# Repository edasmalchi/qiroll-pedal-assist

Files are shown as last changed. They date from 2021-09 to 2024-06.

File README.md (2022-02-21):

# qiroll-pedal-assist
#### External pedal-assist system for Qiroll ebike kit, implemented with CMOS digital logic

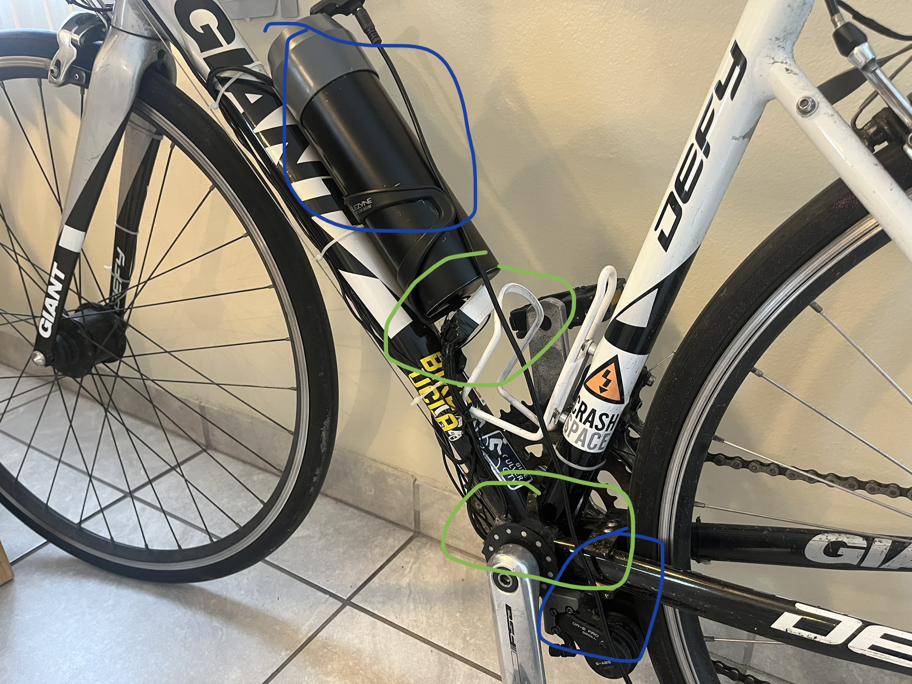
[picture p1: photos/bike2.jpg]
bike


So I got this Qiroll friction-drive ebike kit  to put on my commuter bike. I'd reccomend the [pro](https://www.aliexpress.com/item/1005002975061464.html) [version](https://www.ebay.com/itm/Electric-Bicycle-E-BIKE-Conversion-Kit-QiROLL-Friction-Drive-QR-E-PRO-H70/402658347675) (about $600 shipped), but the standard [kit](https://www.aliexpress.com/item/4000366510773.html) (about $450 shipped) is still around. With light pedaling, the pro version on my bike cruises at about 23mph with about 20 miles of range, while the standard kit delivers about 19mph and about 20 miles (with the larger B70 battery).

The lack of any sort of pedal assist bothered me, with the original design you have to hold down a switch to keep the motor on. (It's a simple switch, not a real throttle so the motor is either on or off. There is a way to select between a lower power mode and a higher power mode.)

This project aims to add pedal assist functionality to the Qiroll kit. I'm using this 12-magnet pedal assist [sensor](https://smile.amazon.com/gp/product/B08GY819YF/), although similar products could work too. The project also supports an optional brake sensor, I'm using [this one](https://www.aliexpress.com/item/4000445394702.html) but others likely work as well. Be sure to verify proper operation in case yours works differently.

#### Hardware Mods
* Since my design needs only one button, with single-clicks turning pedal assist on/off and double-clicks switching controller modes (and/or enabling regen), I didn't need the second button in the original Qiroll switch. So I desoldered it, and used the space/wiring for a resistor and an led that lines up nicely with the hole left by taking the button out, letting me see if pedal assist is currently on or off!

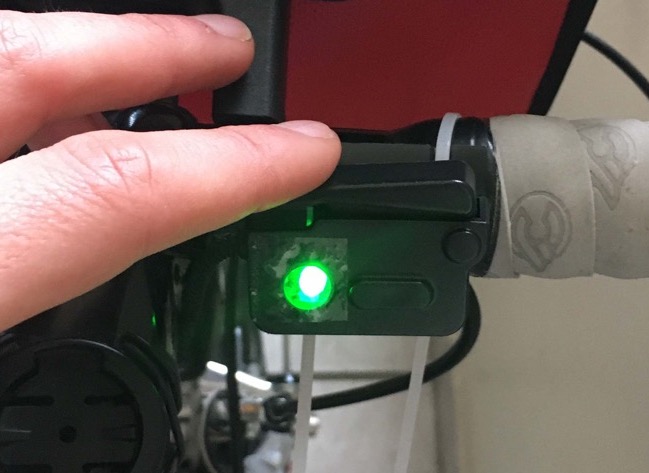
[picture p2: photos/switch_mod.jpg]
switch with LED added


* Stripped the insulation and soldered into one of the battery wires to tap power-- should be fine since the pedal assist system uses very little current but be careful not to damage the battery wire itself. Alternatively you could get some of those Amass connectors it uses and make an adaptor.
* Depending on your setup, cable strain at the battery connector seems to be an issue. Reccomend adding extra strain relief here, and consider tapping at the motor connection instead since splicing in another wire with solder does weaken things.

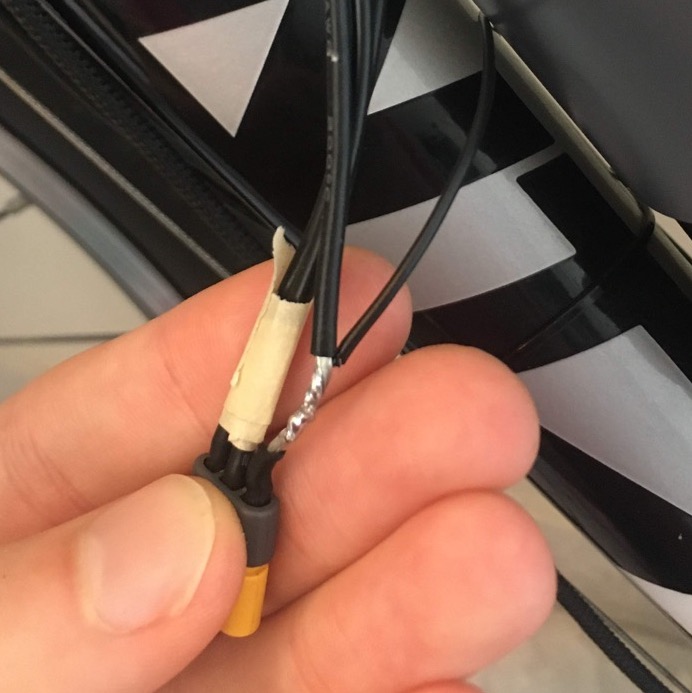
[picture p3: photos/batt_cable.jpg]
battery cable showing small wire soldered to + wire


#### Notes
* The sensor I got reads in both directions, so it will trigger on backwards pedaling as well. I don't think this is a big deal, but there may be sensors out there that only read in one direction.
* After much investigation, the power from the Qiroll micro-usb switch port seems to fluctuate quite a bit. So the reliable thing to do is tap into the + side of the battery, using a linear voltage regulator (or buck converter) to drop down the battery voltage.
* ___Use at your own risk! I reccomend extensive testing of whatever implementation you come up with, ensuring your brakes can stop the bike even if the motor sticks on, and having the battery cable within reach to disconnect if necessary!___

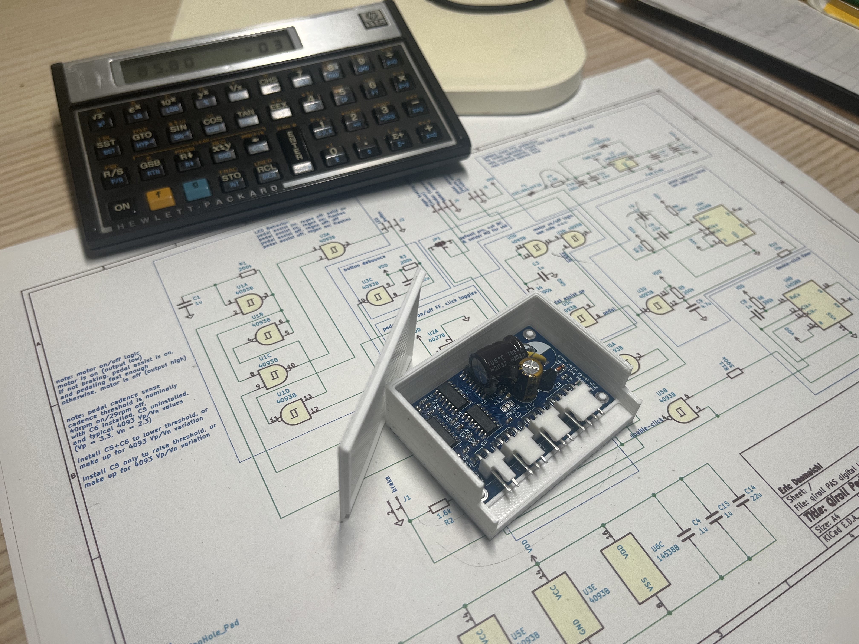
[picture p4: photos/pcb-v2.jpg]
pcb


#### Progress
* Digital logic version 2.5 builds on 2.2 with usability improvements and taillight connector option
* A simple case for 3d printing
* Stripped-down "simple" digital logic version with through-hole components in case that better meets your needs

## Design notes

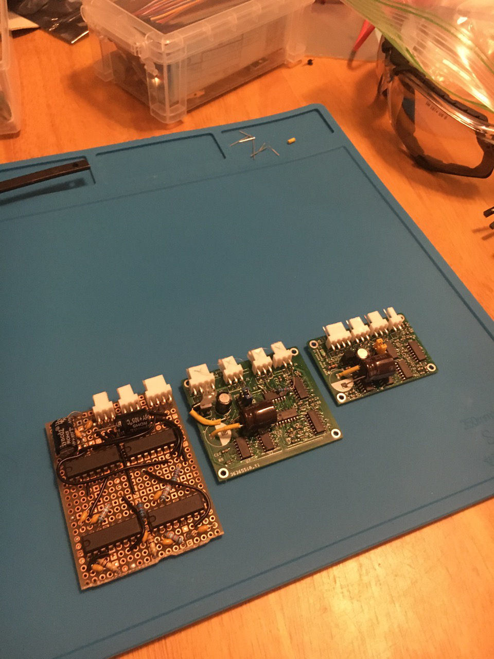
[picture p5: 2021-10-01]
photos/evolution.jpg

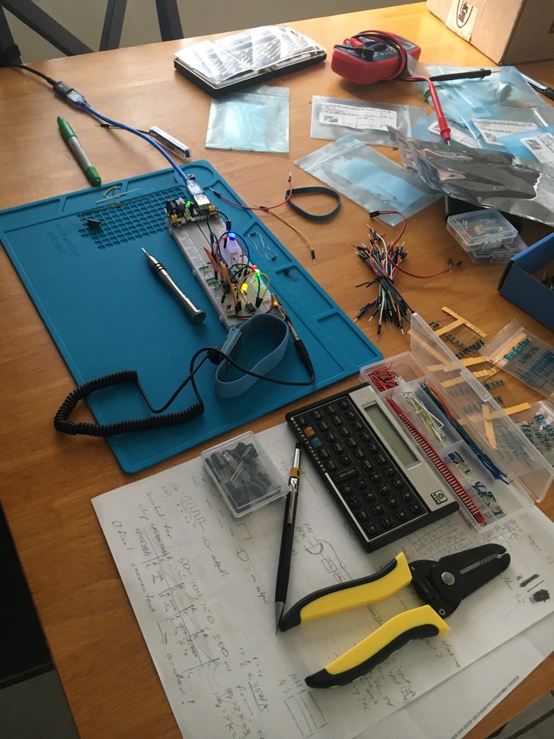
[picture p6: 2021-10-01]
photos/workstation.jpg

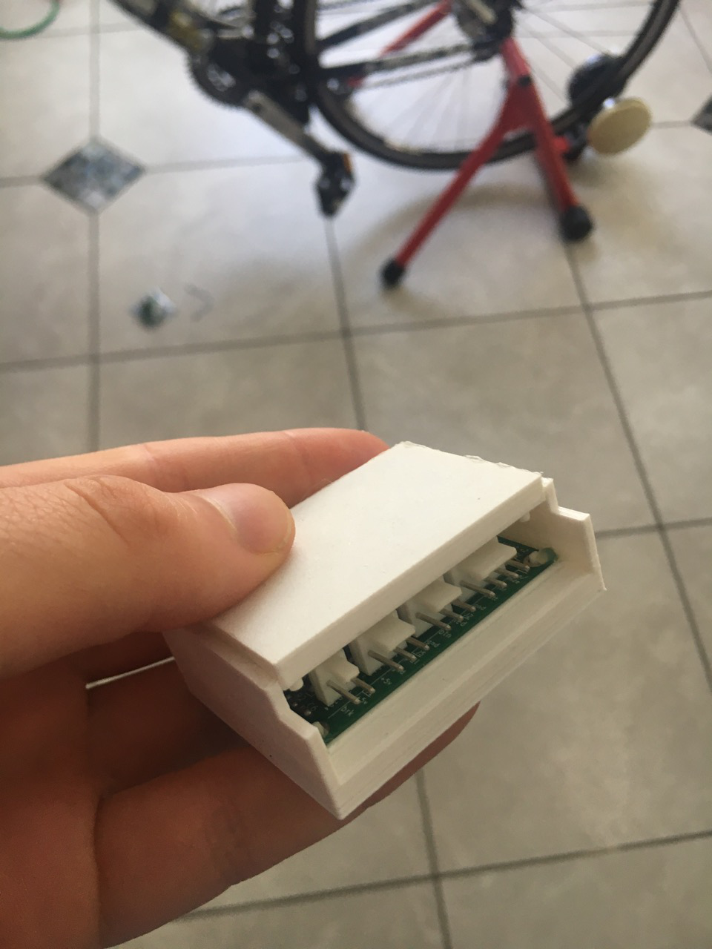
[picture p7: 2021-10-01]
photos/case.jpg

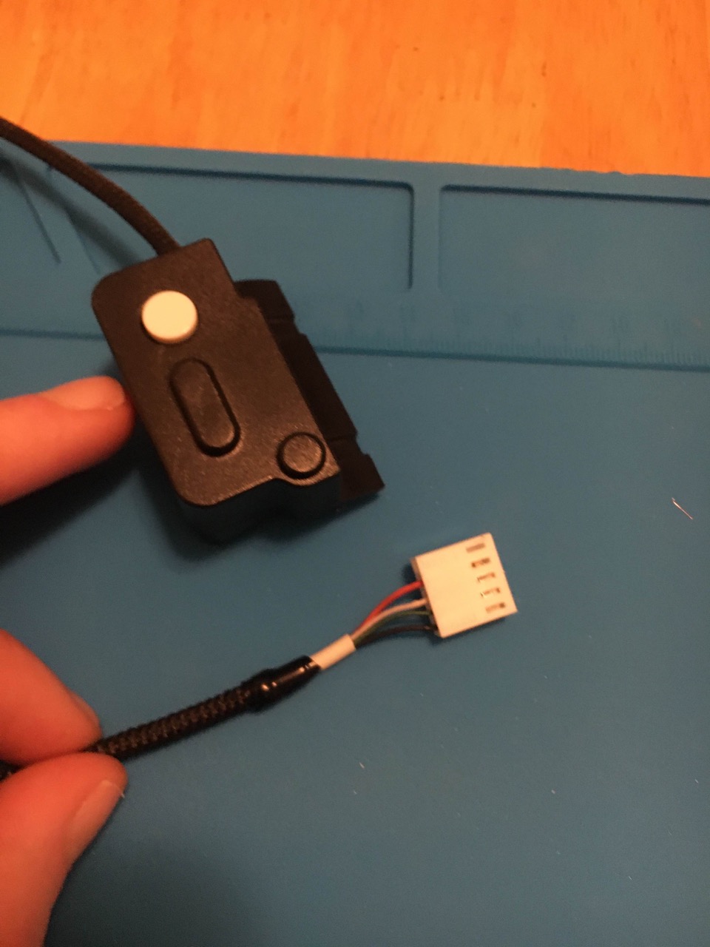
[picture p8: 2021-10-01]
photos/switch.jpg

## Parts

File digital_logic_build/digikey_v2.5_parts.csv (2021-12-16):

Country of Origin may be different at time of shipment.
The HTSUS and ECCN information shown is for informational purposes only and is not a representation or warranty as to the accuracy or reliability of these classifications. All information is provided "as is" and is subject to change without notice. Any use made of the information provided is without recourse to Digi-Key and at the user's risk.
Index | Manufacturer Part Number | Manufacturer Name | Description | Availability | Stock Status | Attrition % | Requested Quantity 1 | Pack Quantity 1 | Pack Type 1 | Digi-Key Part Number 1 | Unit Price 1 | Extended Price 1 | Minimum Order Quantity 1 | Customer Reference | Requested Part Number | Lead Weeks | Datasheet | Reference Designator | US Import Tariff | Note | Part Status | RoHS Status | ECCN | HTSUS | Country of Origin | Environmental Information | Original Part numbers | Image
1 | EMK107BJ104KAHT | Taiyo Yuden | CAP CER 0.1UF 16V X5R 0603 | 192,228 | In Stock |  | 4 | 4 | Cut Tape (CT) | 587-3308-1-ND | 0.10000 | $0.40 | 1 |  | EMK107BJ104KAHT | 44 | https://ds.yuden.co.jp/TYCOMPAS/ut/detail?pn=EMK107BJ104KAHT &u=M |  | May apply on shipments to the U.S. |  | Active | ROHS3 Compliant | EAR99 | 8532.24.0020 | China |  | EMK107BJ104KAHT | //media.digikey.com/Renders/Taiyo%20Yuden%20Renders/0603-(1608-Metric)-0,95mm.jpg
2 | UPS1H151MPD | Nichicon | CAP ALUM 150UF 20% 50V RADIAL | 2 | In Stock |  | 1 | 1 | Bulk | 493-17152-ND | 0.80000 | $0.80 | 1 |  | 493-17152-ND | 63 | https://www.nichicon.co.jp/english/products/pdfs/e-ups.pdf |  | N/A |  | Active | ROHS3 Compliant | EAR99 | 8532.22.0020 | Malaysia |  | 493-17152-ND | //media.digikey.com/Photos/Nichicon%20Photos/PS%20Series%2010mm.jpg
3 | UFW0J471MED | Nichicon | CAP ALUM 470UF 20% 6.3V RADIAL | 2,877 | In Stock |  | 1 | 1 | Bulk | 493-15113-ND | 0.35000 | $0.35 | 1 |  | 493-15113-ND | 72 | https://www.nichicon.co.jp/english/products/pdfs/e-ufw.pdf |  | N/A |  | Active | ROHS3 Compliant | EAR99 | 8532.22.0020 | - |  | 8AX200MEFC6-3X7 | //media.digikey.com/Photos/Nichicon%20Photos/FW-SERIES-6.jpg
4 | 0022053041 | Molex | CONN HEADER R/A 4POS 2.54MM | 5,920 | In Stock |  | 2 | 2 | Bulk | WM4302-ND | 0.59000 | $1.18 | 1 |  | WM4302-ND | 33 | https://www.molex.com/pdm_docs/sd/022053041_sd.pdf |  | N/A |  | Active | ROHS3 Compliant | EAR99 | 8536.69.4040 | India | https://www.molex.com/datasheets/rohspdf/0022053041_rohs.pdf | WM4302-ND | //media.digikey.com/photos/Molex/22-05-3041.jpg
5 | 0010112043 | Molex | CONN HOUSING 4POS .100 HI PRESS | 37,198 | In Stock |  | 2 | 2 | Bag | WM2603-ND | 0.23000 | $0.46 | 1 |  | WM2603-ND | 33 | https://www.molex.com/pdm_docs/sd/010112043_sd.pdf |  | N/A |  | Active | ROHS3 Compliant | EAR99 | 8536.69.8000 | India | https://www.molex.com/datasheets/rohspdf/0010112043_rohs.pdf | WM2603-ND | //media.digikey.com/photos/Molex/10-11-2043.jpg
6 | 0022053031 | Molex | CONN HEADER R/A 3POS 2.54MM | 69,023 | In Stock |  | 2 | 2 | Bag | WM4301-ND | 0.46000 | $0.92 | 1 |  | 0022053031 | 33 | https://www.molex.com/pdm_docs/sd/022053031_sd.pdf |  | N/A |  | Active | ROHS3 Compliant | EAR99 | 8536.69.4040 | India | https://www.molex.com/datasheets/rohspdf/0022053031_rohs.pdf | 0022053031 | //media.digikey.com/photos/Molex/22-05-3031.jpg
7 | 0010112034 | Molex | CONN HOUSING 3 POS | 32,495 | In Stock |  | 2 | 2 | Bag | 0010112034-ND | 0.20000 | $0.40 | 1 |  | 0010112034 | 33 | https://www.molex.com/pdm_docs/sd/010112034_sd.pdf |  | N/A |  | Active | ROHS3 Compliant | EAR99 | 8536.69.8000 | India |  | 0010112034 | //media.digikey.com/Photos/Molex/0010112034.jpg
8 | ERJ-3EKF2003V | Panasonic Electronic Components | RES SMD 200K OHM 1% 1/10W 0603 | 3,045 | In Stock |  | 3 | 3 | Cut Tape (CT) | P200KHCT-ND | 0.10000 | $0.30 | 1 |  | P200KHCT-ND | 52 | https://industrial.panasonic.com/cdbs/www-data/pdf/RDA0000/AOA0000C304.pdf |  | May apply on shipments to the U.S. |  | Active | ROHS3 Compliant | EAR99 | 8533.21.0030 | China | https://industrial.panasonic.com/cdbs/www-cgi/auto-publishing.cgi?type=ROSU&region=WW&layer=4&cd=AOA0002 | ERJ-3GEYJ204V | //media.digikey.com/Photos/Panasonic%20Photos/MFG_ERJ-P6W%20Series.jpg
9 | ERJ-3GEYJ394V | Panasonic Electronic Components | RES SMD 390K OHM 5% 1/10W 0603 | 38,772 | In Stock |  | 4 | 4 | Cut Tape (CT) | P390KGCT-ND | 0.10000 | $0.40 | 1 |  | ERJ-3GEYJ394V | 29 | https://industrial.panasonic.com/ww/products/pt/general-purpose-chip-resistors/models/ERJ3GEYJ394V |  | May apply on shipments to the U.S. |  | Active | ROHS3 Compliant | EAR99 | 8533.21.0030 | China | https://industrial.panasonic.com/cdbs/www-cgi/auto-publishing.cgi?type=ROSU&region=WW&layer=4&cd=AOA0002 | ERJ-3GEYJ394V | //media.digikey.com/Photos/Panasonic%20Photos/MFG_ERJ-P6W%20Series.jpg
10 | MC14538BDR2G | onsemi | IC MULTIVIBRATOR 95NS 16SOIC | 37,817 | In Stock |  | 1 | 1 | Cut Tape (CT) | MC14538BDR2GOSCT-ND | 0.77000 | $0.77 | 1 |  | MC14538BDR2GOSCT-ND | 40 | https://www.onsemi.com/pdf/datasheet/mc14538b-d.pdf |  | May apply on shipments to the U.S. |  | Active | ROHS3 Compliant | EAR99 | 8542.39.0001 | China | https://www.onsemi.com/site/pdf/RoHS-statement.pdf|https://www.onsemi.com/PowerSolutions/MaterialComposition.do?export=pdf&opnId=MC14538BDR2G | MC14538BDR2GOSCT-ND | //media.digikey.com/Renders/On%20Semi%20Renders/488~751B-05~D,-VD,-FD~16.JPG
11 | CD4027BM96 | Texas Instruments | IC FF JK TYPE DUAL 1BIT 16SOIC | 4,633 | In Stock |  | 1 | 1 | Cut Tape (CT) | 296-31493-1-ND | 0.58000 | $0.58 | 1 |  | CD4027BM96 | 6 | https://www.ti.com/general/docs/suppproductinfo.tsp?distId=10 |  | N/A |  | Active | ROHS3 Compliant | EAR99 | 8542.39.0001 | - |  | CD4027BM96 | //media.digikey.com/Renders/~~Pkg.Case%20or%20Series/16%20SOIC.jpg
12 | EMK107BJ105KAHT | Taiyo Yuden | CAP CER 1UF 16V X5R 0603 | 1,451 | In Stock |  | 3 | 3 | Cut Tape (CT) | 587-3309-1-ND | 0.10000 | $0.30 | 1 |  | EMK107BJ105KAHT | 32 | https://ds.yuden.co.jp/TYCOMPAS/ut/detail?pn=EMK107BJ105KAHT &u=M |  | May apply on shipments to the U.S. |  | Active | ROHS3 Compliant | EAR99 | 8532.24.0020 | China |  | EMK107BJ105KAHT | //media.digikey.com/Renders/Taiyo%20Yuden%20Renders/0603-(1608-Metric)-0,95mm.jpg
13 | ERJ-3GEYJ753V | Panasonic Electronic Components | RES SMD 75K OHM 5% 1/10W 0603 | 29,117 | In Stock |  | 4 | 4 | Cut Tape (CT) | P75KGCT-ND | 0.10000 | $0.40 | 1 |  | ERJ-3GEYJ753V | 29 | https://industrial.panasonic.com/ww/products/pt/general-purpose-chip-resistors/models/ERJ3GEYJ753V |  | May apply on shipments to the U.S. |  | Active | ROHS3 Compliant | EAR99 | 8533.21.0030 | China | https://industrial.panasonic.com/cdbs/www-cgi/auto-publishing.cgi?type=ROSU&region=WW&layer=4&cd=AOA0002 | ERJ-3GEYJ753V | //media.digikey.com/Photos/Panasonic%20Photos/MFG_ERJ-P6W%20Series.jpg
14 | JMK107BJ475KA-T | Taiyo Yuden | CAP CER 4.7UF 6.3V X5R 0603 | 590,918 | In Stock |  | 1 | 1 | Cut Tape (CT) | 587-1785-1-ND | 0.12000 | $0.12 | 1 |  | 587-1785-1-ND | 44 | https://ds.yuden.co.jp/TYCOMPAS/ut/detail?pn=JMK107BJ475KA-T &u=M |  | May apply on shipments to the U.S. |  | Not For New Designs | ROHS3 Compliant | EAR99 | 8532.24.0020 | China |  | 587-1785-1-ND | //media.digikey.com/Renders/Taiyo%20Yuden%20Renders/0402%20(1005%20Metric).jpg
15 | EMK107B7224KA-T | Taiyo Yuden | CAP CER 0.22UF 16V X7R 0603 | 50,940 | In Stock |  | 3 | 3 | Cut Tape (CT) | 587-1249-1-ND | 0.10000 | $0.30 | 1 |  | EMK107B7224KA-T | 32 | https://ds.yuden.co.jp/TYCOMPAS/ut/detail?pn=EMK107B7224KA-T &u=M |  | May apply on shipments to the U.S. |  | Not For New Designs | ROHS3 Compliant | EAR99 | 8532.24.0020 | China |  | EMK107B7224KA-T | //media.digikey.com/Renders/Taiyo%20Yuden%20Renders/0603-(1608-Metric)-0,95mm.jpg
16 | CD4093BM96 | Texas Instruments | IC GATE NAND 4CH 2-INP 14SOIC | 24,961 | In Stock |  | 3 | 3 | Cut Tape (CT) | 296-25956-1-ND | 0.58000 | $1.74 | 1 |  | 296-25956-1-ND | 35 | https://www.ti.com/general/docs/suppproductinfo.tsp?distId=10 |  | N/A |  | Active | ROHS3 Compliant | EAR99 | 8542.39.0001 | Malaysia |  | 296-25956-1-ND | //media.digikey.com/Renders/Texas%20Instr%20Renders/296;-4040047-5;-D;-14.jpg
17 | FDLL4148-D87Z | onsemi | DIODE GEN PURP 100V 200MA SOD80 | 8,443 | In Stock |  | 1 | 1 | Cut Tape (CT) | FDLL4148-D87ZCT-ND | 0.10000 | $0.10 | 1 |  | FDLL4148-D87Z | 36 | https://rocelec.widen.net/view/pdf/bhc41r7lwc/ONSM-S-A0003539415-1.pdf?t.download=true&u=5oefqw |  | May apply on shipments to the U.S. |  | Active | ROHS3 Compliant | EAR99 | 8541.10.0070 | - | https://www.onsemi.com/PowerSolutions/MaterialComposition.do?export=pdf&opnId=FDLL4148-D87Z|https://www.onsemi.com/site/pdf/RoHS-statement.pdf | FDLL4148-D87Z | //media.digikey.com/photos/Fairchild%20Semi%20Photos/261-LL-34%20FD.jpg
18 | 0ZCJ0012FF2E | Bel Fuse Inc. | PTC RESET FUSE 48V 120MA 1206 | 19,958 | In Stock |  | 1 | 1 | Cut Tape (CT) | 507-1795-1-ND | 0.12000 | $0.12 | 1 |  | 507-1795-1-ND | 20 | https://www.belfuse.com/resources/datasheets/circuitprotection/ds-cp-0zcj-series.pdf |  | N/A |  | Active | ROHS3 Compliant | EAR99 | 8533.40.8070 | Taiwan | https://belfuse.com/resource-center/quality-environmental/documents/bel%20fuse/environmental/Declaration%20of%20EU%20RoHS%20Compliance.pdf|https://belfuse.com/resource-center/quality-environmental/documents/bel%20fuse/environmental/REACH%20SVHC%20201%20Declaration.pdf | 0ZCJ0012FF2E | //media.digikey.com/Renders/Bel%20Fuse%20Renders/0ZCK-Series-1206.jpg
19 | GRM188R60J226MEA0D | Murata Electronics | CAP CER 22UF 6.3V X5R 0603 | 131,325 | In Stock |  | 1 | 1 | Cut Tape (CT) | 490-7611-1-ND | 0.23000 | $0.23 | 1 |  | 490-7611-1-ND | 23 | https://www.murata.com/-/media/webrenewal/support/library/catalog/products/capacitor/ceramiccapacitor/c02e.ashx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 |  | N/A |  | Active | ROHS3 Compliant | EAR99 | 8532.24.0020 | Japan |  | 490-7611-1-ND | //media.digikey.com/Renders/Murata%20Renders/0603-(1608-Metric)-1,00mm.jpg
20 | MCP1799T-3302H/TT | Microchip Technology | IC REG LINEAR 3.3V 80MA SOT23-3 | 170 | In Stock |  | 1 | 1 | Cut Tape (CT) | 150-MCP1799T-3302H/TTCT-ND | 0.46000 | $0.46 | 1 |  | 150-MCP1799T-3302H/TTCT-ND | 5 | http://ww1.microchip.com/downloads/en/DeviceDoc/MCP1799-Data-Sheet-20006248A.pdf |  | N/A |  | Active | ROHS3 Compliant | EAR99 | 8542.39.0001 | Thailand |  | 150-MCP1799T-3302H/TTCT-ND | //media.digikey.com/Renders/Microchip%20Tech%20Renders/SOT-23-3%20PKG.jpg
21 | RB751S40T1G | onsemi | DIODE SCHOTTKY 30V 30MA SOD523 | 64,699 | In Stock |  | 4 | 4 | Cut Tape (CT) | RB751S40T1GOSCT-ND | 0.21000 | $0.84 | 1 |  | RB751S40T1G | 53 | https://www.onsemi.cn/pdf/datasheet/rb751s40t1-d.pdf |  | May apply on shipments to the U.S. |  | Active | ROHS3 Compliant | EAR99 | 8541.10.0070 | - | https://www.onsemi.com/PowerSolutions/MaterialComposition.do?export=pdf&opnId=RB751S40T1G|https://www.onsemi.com/site/pdf/RoHS-statement.pdf | RB751S40T1G | //media.digikey.com/Renders/On%20Semi%20Renders/SOD-523_502.jpg
22 | ESR03EZPJ332 | Rohm Semiconductor | RES SMD 3.3K OHM 5% 1/4W 0603 | 144,013 | In Stock |  | 1 | 1 | Cut Tape (CT) | RHM3.3KDCT-ND | 0.10000 | $0.10 | 1 |  | ESR03EZPJ332 | 52 | https://fscdn.rohm.com/en/products/databook/datasheet/passive/resistor/chip_resistor/esr-e.pdf |  | N/A |  | Active | ROHS3 Compliant | EAR99 | 8533.21.0030 | Philippines |  | ESR03EZPJ332 | //media.digikey.com/Renders/Rohm%20Renders/ESR01.jpg

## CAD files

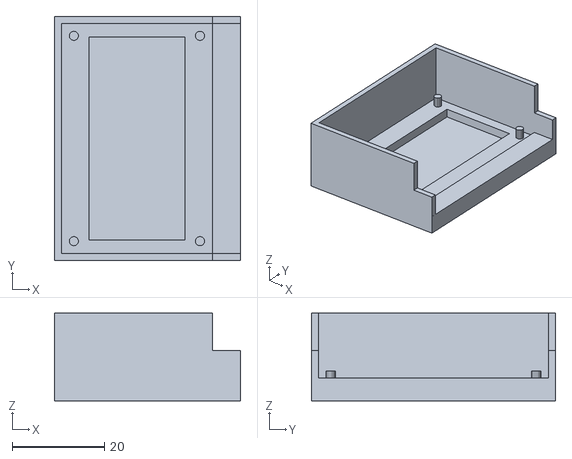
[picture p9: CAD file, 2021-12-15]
digital_logic_build_simple/case/bottom_case.stl
40.3 x 52.9 x 19.0

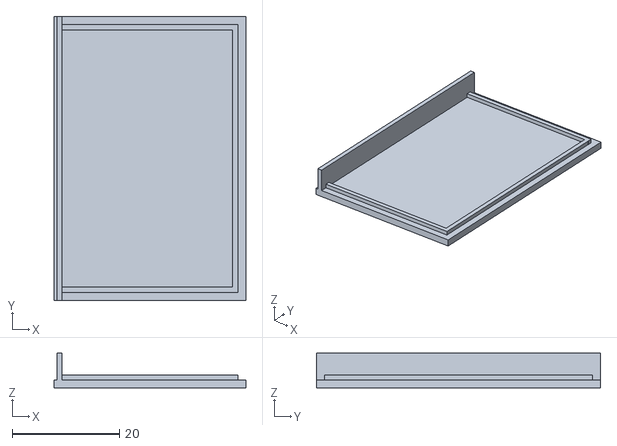
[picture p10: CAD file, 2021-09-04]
digital_logic_build_simple/case/top_case.stl
35.8 x 53.0 x 6.50

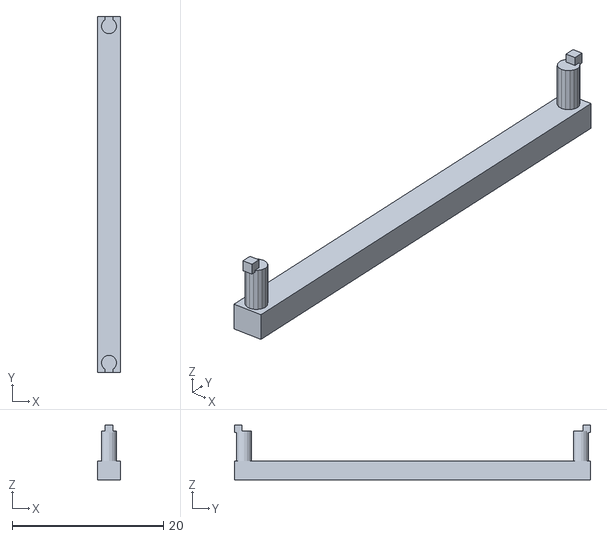
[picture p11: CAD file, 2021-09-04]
digital_logic_build_simple/case/case_test.stl
3.00 x 47.0 x 7.25

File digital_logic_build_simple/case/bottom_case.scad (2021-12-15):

$fa = 1;
$fs = 0.4;
//translate([0, 22, 0])
// bottom of case
x = 32.8;
y = 50;
cube([x,y,1.5],center=true);

//tht bump + pegs
translate([(x/2)-3.001,0,3.1-1.26])
    cube([6,y,2.5],center=true);
translate([27.3/2,22.225,4.5-1.26])
    cylinder(h=5,r=1, center=true);
//translate([0,23,5.7-.2]) no need for retention cubes?
//    cube([1, 1, 1], center=true);
translate([27.3/2,-22.225,4.5-1.26])
    cylinder(h=5,r=1, center=true);
//translate([0,-23,5.7-.2]) no need for retention cubes?
//    cube([1, 1, 1], center=true);
    
    //tht bump + pegs
translate([-((x/2)-3.001),0,3.1-1.26])
    cube([6,y,2.5],center=true);
translate([-27.3/2,22.225,4.5-1.26])
    cylinder(h=5,r=1, center=true);
//translate([0,23,5.7-.2]) no need for retention cubes?
//    cube([1, 1, 1], center=true);
translate([-27.3/2,-22.225,4.5-1.26])
    cylinder(h=5,r=1, center=true);
//translate([0,-23,5.7-.2]) no need for retention cubes?
//    cube([1, 1, 1], center=true);

//side supports
translate([0,-((y/2)-1.501),3.1-1.26])
cube([x,3,2.5],center=true);

translate([0,((y/2)-1.501),3.1-1.26])
cube([x,3,2.5],center=true);

//sides
translate([0,((y/2)+.699),10-1.26])
cube([x,1.5,19],center=true);

translate([0,-((y/2)+.699),10-1.26])
cube([x,1.5,19],center=true);
//back
translate([-((x/2)+.69),0,10-1.26])
cube([1.5,y+2.9,19],center=true);

//front lip
//translate([((x/2)+0.49),0,3.5-1.26])
//cube([1,y+2.9,6],center=true);
//snout
translate([((x/2)+3.0),0,3-1.26])
cube([6.05,y+2.9,5],center=true);

translate([3,((y/2)+.699),7.5-1.26])
cube([x+6,1.5,7.8],center=true);

translate([3,-((y/2)+.699),7.5-1.26])
cube([x+6,1.5,7.8],center=true);

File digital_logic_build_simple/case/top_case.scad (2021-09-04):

$fa = 1;
$fs = 0.4;
//translate([0, 22, 0])
// top of case
x = 32.8;
y = 50;
cube([x+3,y+3,1.5],center=true);

translate([-((x/2)+.499),0,3-.25])
cube([1,y+3,6], center=true);

translate([((x/2)-.501),0,1])
cube([1,y,1.25], center=true);
translate([0,-((y/2)-.501),1])
cube([x,1,1.25], center=true);
translate([0,((y/2)-.501),1])
cube([x,1,1.25], center=true);

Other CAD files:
digital_logic_build_simple/case/case_test.scad

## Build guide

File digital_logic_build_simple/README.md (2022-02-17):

# Digital logic version (simple)

Built from some 4000-series CMOS chips, this design implements pedal assist for the Qiroll kit. Single click turns PAS on/off, double-click turns regen on/off (pro) or changes modes (standard). Triple-click changes modes with the pro, must be stopped.

### Notes
* Does not support regen LED flash or latching regen on the Pro kit (brake sensor simple regen still an option)

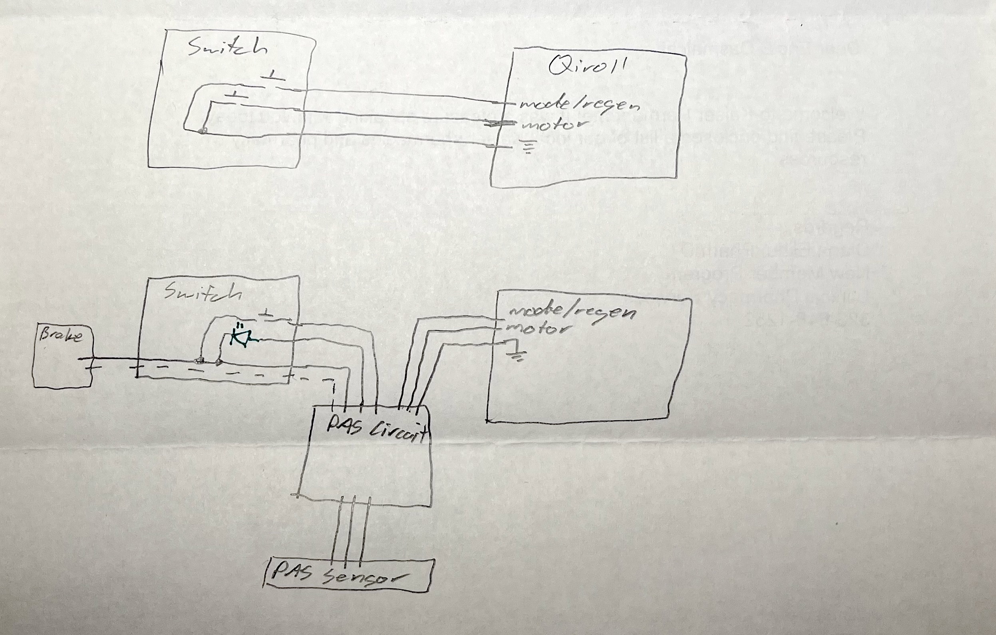
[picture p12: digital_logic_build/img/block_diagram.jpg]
switch with LED added


_Illustration of the Qiroll kit without the circuit (top), and how the circuit interfaces (bottom)_

### Build it!
* most parts have a DigiKey or at least a datasheet link if you open the schematic in KiCad and click the "edit symbol fields" icon (4th from right at top)

### Test it!
* check the board visually for solder joint quality
* _at minimum, verify the battery + voltage is not shorted to anything with a multimeter before connecting to the battery_
* consider functional testing using LEDs to view signals on a breadboard and some sort of square wave generator (you could use a CMOS 555 or 4047B at 3.3v) to stand in for the PAS sensor

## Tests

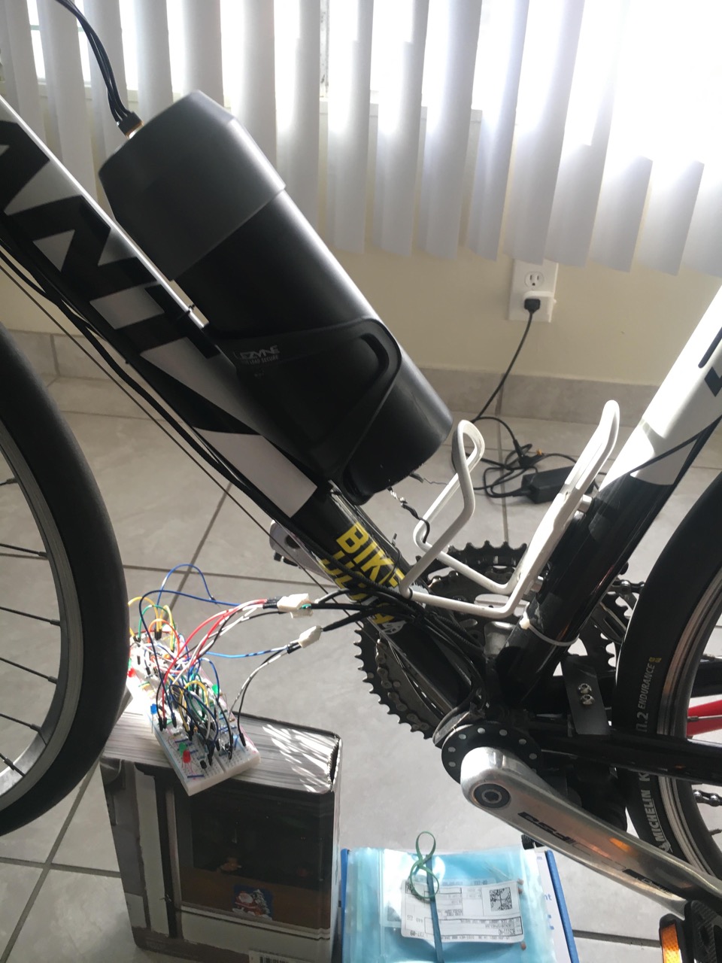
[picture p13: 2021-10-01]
photos/logic_testing.jpg

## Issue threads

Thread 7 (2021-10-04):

digital logic: pedal assist mode and/or regen turns on/off without switch input

edasmalchi, 2021-10-04:
What?

Both modules of 4027B JK flip-flop U2 switch states intermittently without pressing or double-clicking the switch.

Actions

- [x] Inspect all connectors
- [x] Test stability with regen/mode and motor outputs disconnected
- [x] Test adding 1uf decoupling per chip
- [ ] Connect to ground at battery, not motor
- [ ] Assess VDD, ground, relevant logic signals using oscilloscope

Closed 2021-12-17.

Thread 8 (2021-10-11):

digital logic: PCB v2.1

edasmalchi, 2021-10-11:
- [x] Solder jumpers for pro/std instead of header pins, with pro jumper being NC
- [x] Additional decoupling/other changes identified in debug process

edasmalchi, 2021-10-18:
V2.2 ordered from JLCPCB!

Closed 2021-10-18.

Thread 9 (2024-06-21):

Thank you

c0d3z3r0, 2024-06-21:
Man, awesome! That's exactly what I was thinking about when ordering a Qiroll Pro today :smile:
While I'm going to do it with a uC, I still really like your non-uC approach!

I wonder, if you tried to find a way to select normal vs. power mode on the Pro while driving?
Maybe there's a way to hack the firmware, but the problem seems the PCB being filled up with epoxy :/

edasmalchi, 2024-06-21:
Nice, yeah I think it makes the Qiroll a lot better. And sadly no, but I suspect you’re right that it would require getting at that PCB…

I think Qiroll is a good product overall, still surprises me that they haven’t added pedal assist.

happy riding!

c0d3z3r0, 2024-06-23:
It's a bit weird that the note at the picture and text disagree....
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

It seems they have fixed this with version 2:

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

You mentioned that the output voltage on the "USB" port is fluctuating. Do you remember what voltage it was exactly?

edasmalchi, 2024-06-23:
Interesting!So I didn’t know much about electronics when I started this (still not an expert by any means!). I think it’s 5v… but not actually intended to source current so it bounces all over even with a small load (maybe it’s just pulled high by their uC the way I assume the two buttons are?). Without knowing what’s going on in there it’s hard to be certain…On Jun 23, 2024, at 05:15, Michael Niewöhner ***@***.***> wrote:
It's a bit weird that the note at the picture and text disagree....
image.png (view on web)
It seems they have fixed this with version 2:
image.png (view on web)
You mentioned that the output voltage on the "USB" port is fluctuating. Do you remember what voltage it was exactly?

—Reply to this email directly, view it on GitHub, or unsubscribe.You are receiving this because you commented.Message ID: ***@***.***>

c0d3z3r0, 2024-06-24:
Ok, let's see what I can find out when I get mine :-)

Do you have a photo of the switch PCB by chance?

edasmalchi, 2024-06-24:
Sure, it's the older version. Real simple, just a ground and one signal per switch.

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

c0d3z3r0, 2024-07-13:
Sooooooo I got my hands an a defective Qiroll Pro v2. Epoxy can't stop me haha, so I managed to get the (now definitely broken) PCB out of it :laughing: Guess what? There's TWO microcontrollers in there \o/ ESP32-C and APM32F303 (STM32F303 clone).

Fortunately, the ESP32 did not have encrypted enabled so I could dump the firmware image. Reverse engineering in progress ;-) Going to dump the APM32 today.

edasmalchi, 2024-07-13:
oh wow! curious to see the results :)

c0d3z3r0, 2024-07-15:
https://github.com/c0d3z3r0/qiroll_rev

edasmalchi, 2024-07-15:
thanks for sharing! will keep an eye on what else you figure out ;)

c0d3z3r0, 2024-07-16:
Oh my.... the APM32 firmware is based on the VESC project... this is going to be fuuuuuuuuun! [vesc-project.com](https://vesc-project.com/)

c0d3z3r0, 2024-07-23:
Just pushed an update ;) It's indeed VESC, version 4.00 to be exact. Yeeeeah. 100% GPL violation -.-

edasmalchi, 2024-07-23:
oh wow ;)

c0d3z3r0, 2024-07-25:
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

:rofl: :rofl: :rofl: :rofl: :rofl: :rofl: :rofl: :rofl: :rofl: :rofl: :rofl: :rofl: :rofl: :rofl: :rofl: :rofl: :rofl:

BluePixel3000, 2025-03-26:
Hi I know I'm a little bit late... My idea is to have the PAS on the motor an being able to convert my bike into an E-Bike with just sliding on the Motor on the adaptor. I'm right now building the PAS sensor with two hall-sensors, an esp8266 (going to step down to a much smaller one) and some simple code wich is working fine. The idea is to have the microcontroller reading out the signals of the hall sensors and "press" the buttons virtually with the ESP itself or controlling transistors... After I read your post here I have some questions:

1. Is it possible to communicate to the microcontroller in the motor via USB and VESC? ( I was not able to replicate.)
2. You mentioned that the Output of the USB is not stable but is it stable enough to power an ESP (is it an option to stabilise the volts with capacitors) ?

Just some extra information my code right now can distinguish between going forward or backward in pedalling to have the option to do the regenerative breaking when paddling backwards. It can also filter out invalid inputs for example adjusting the pedals while standing. Otherwise it would trigger mode switching... To keep the option for mode switching I was thinking about doing it with physical buttons Connected to the ESP on the PAS itself or via Bluetooth with the ESP board.

I you have other ideas or suggestions I would be very happy to hear. :)

Thanks for reading
Best regards form Germany (bad english skill)

edasmalchi, 2025-03-26:
Hi!

> Is it possible to communicate to the microcontroller in the motor via USB and VESC? ( I was not able to replicate.)

Probably not -- I think Qiroll just uses the physical form of the micro-usb connector to provide a ground and two switch inputs without implementing the usb standard itself. It seems @c0d3z3r0 was able to communicate with it after disassembling the board and finding usb via some test pads: https://github.com/c0d3z3r0/qiroll_rev

> You mentioned that the Output of the USB is not stable but is it stable enough to power an ESP (is it an option to stabilise the volts with capacitors) ?

I don't think so, I tried adding up to 500uf of caps when I was trying this and did not find success. But feel free to experiment further.

Your general approach sounds good though. It annoys me a bit that the QR-E Pro apparently does not support mode switching while in motion.

c0d3z3r0, 2025-03-26:
@Blue

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

Correct, the "USB" port is just used as connection port, just like so many other chinese products :/ Check out the schematics here https://github.com/c0d3z3r0/qiroll_rev/blob/master/schematic/qiroll.pdf

BluePixel3000, 2025-04-07:
Hi, I've got some new test results:
As mentioned above, I’m using my own Hall sensors connected to an ESP32 Super Mini. I tested motor control with it, and it works perfectly.

Now for the tricky part: I tapped into the battery wire like @c0d3z3r0 did and connected it to a very small converter. Unfortunately, the power consumption of the ESP and sensors is too low, causing the converter to overheat.

Since using a larger converter wasn’t an option for me, I connected the ESP directly to the 5V pin of the micro USB cable out of frustration – and was surprised when it suddenly worked (yes, without any capacitor!). I’m not sure if this is due to the very low power consumption of the Super Mini or if I have a newer version of the QR Mute E Plus.

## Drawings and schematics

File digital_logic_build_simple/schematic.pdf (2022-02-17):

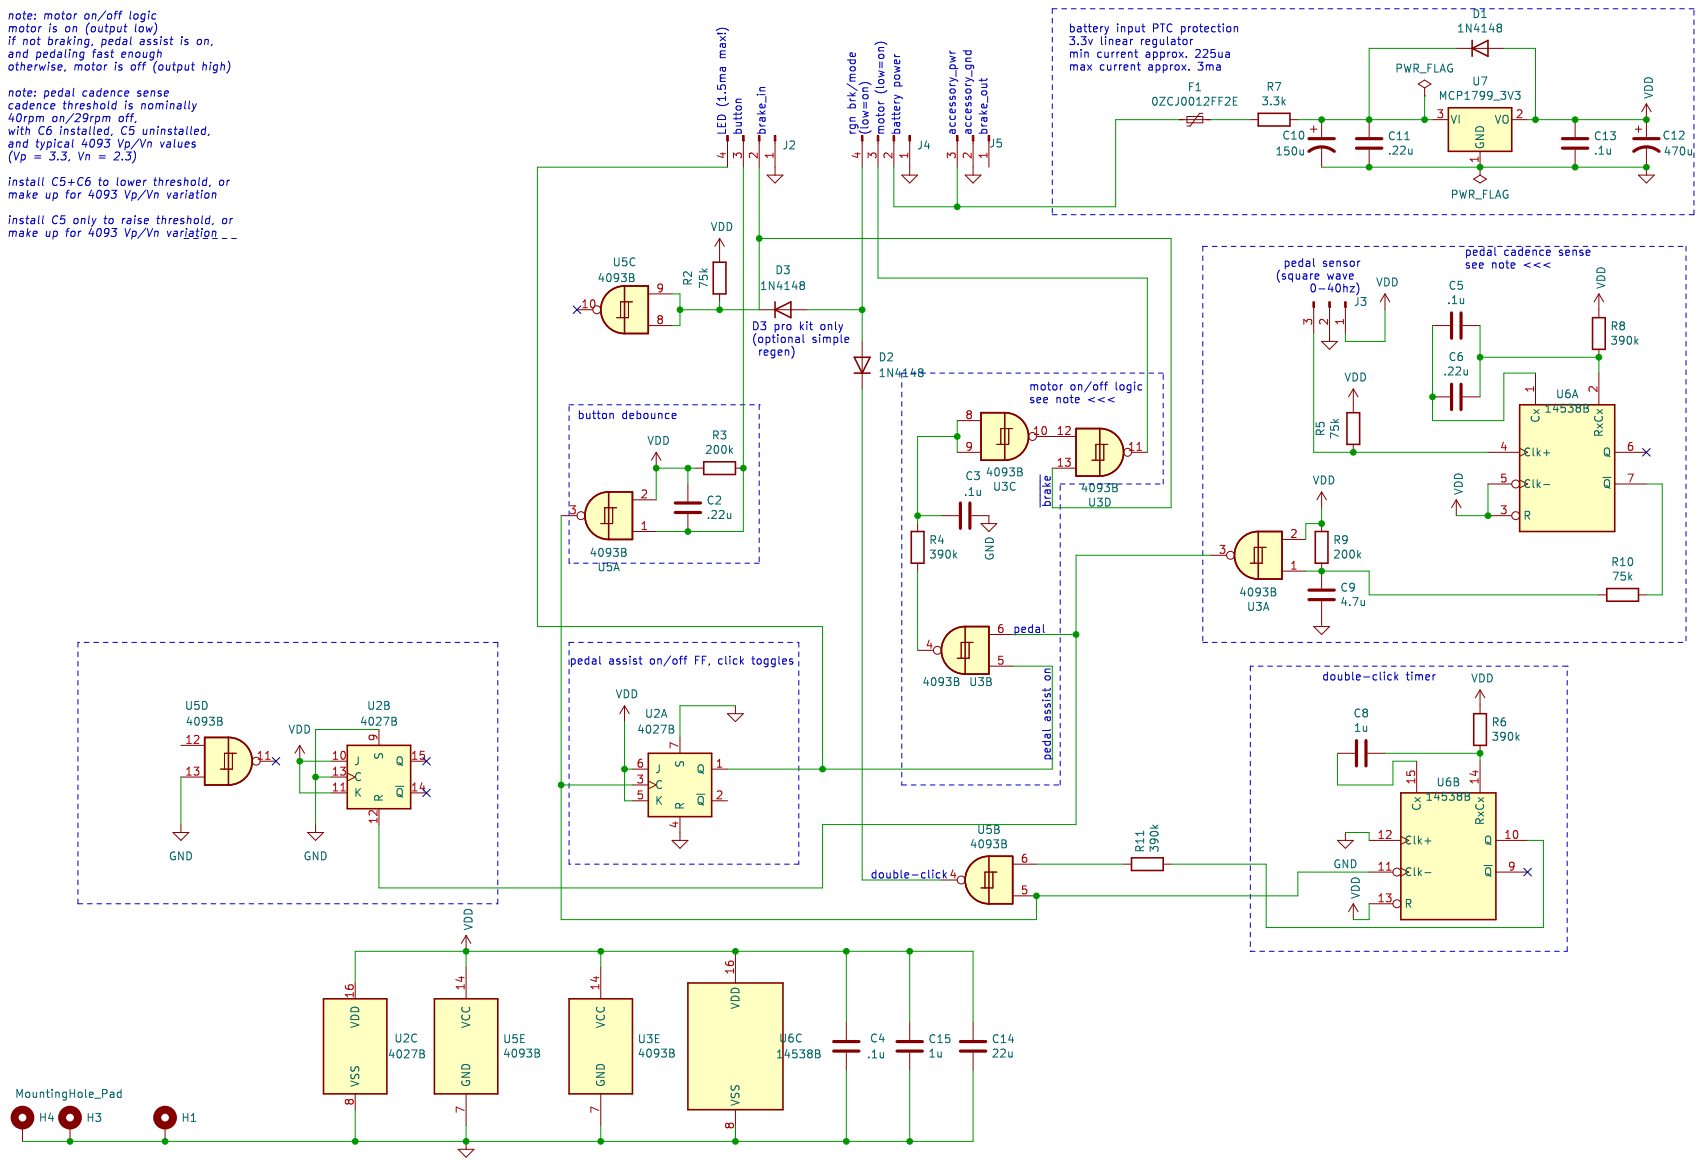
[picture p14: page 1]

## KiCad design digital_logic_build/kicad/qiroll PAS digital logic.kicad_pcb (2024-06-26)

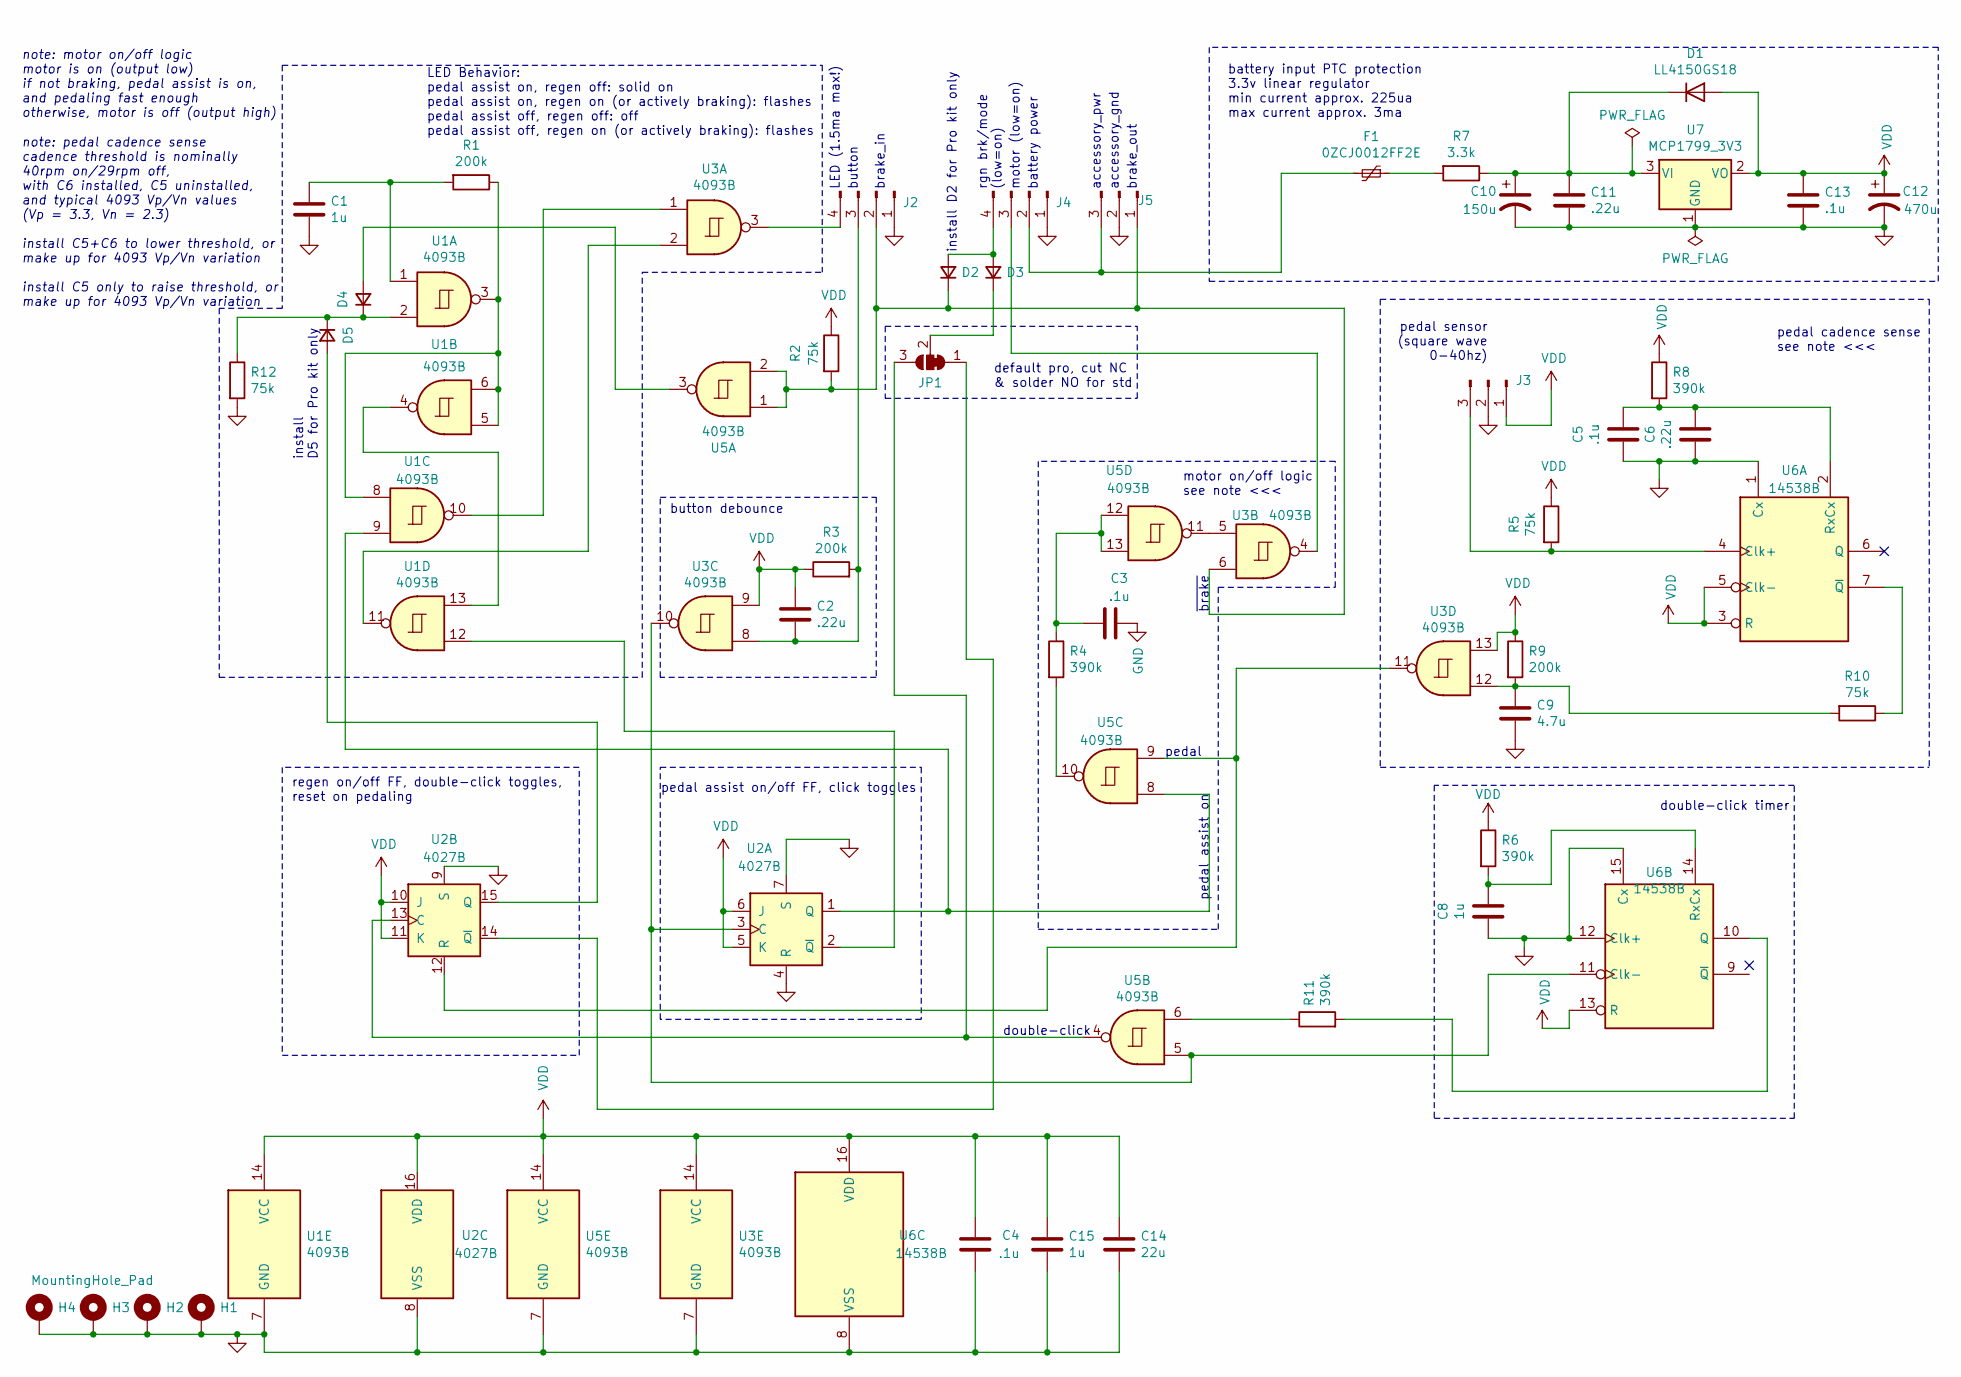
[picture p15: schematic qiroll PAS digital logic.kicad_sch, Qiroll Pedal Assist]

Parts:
C1, C8, C15: 1u; C_0603_1608Metric
C2, C6, C11: .22u; C_0603_1608Metric
C3, C4, C5, C13: .1u; C_0603_1608Metric
C9: 4.7u; C_0603_1608Metric
C10: 150u; CP_Radial_D10.0mm_P5.00mm
C12: 470u; CP_Radial_D6.3mm_P2.50mm
C14: 22u; C_0603_1608Metric
D1: LL4150GS18; D_MiniMELF
D2, D3, D4, D5: D; D_SOD-523
F1: 0ZCJ0012FF2E; Fuse_1206_3216Metric
H1, H2, H3, H4: MountingHole_Pad; MountingHole_2.2mm_M2_DIN965_Pad
J2: led_sw1; PinHeader_1x04_P2.54mm_Vertical
J3: accessory; PinHeader_1x03_P2.54mm_Vertical
J4: mode_thr_batt; PinHeader_1x04_P2.54mm_Vertical
J5: 3_pin; PinHeader_1x03_P2.54mm_Vertical
JP1: SolderJumper_3_Bridged12; SolderJumper-3_P1.3mm_Bridged12_RoundedPad1.0x1.5mm_NumberL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
R1, R3, R9: 200k; R_0603_1608Metric
R2, R5, R10, R12: 75k; R_0603_1608Metric
R4, R6, R8, R11: 390k; R_0603_1608Metric
R7: 3.3k; R_0603_1608Metric
U1, U3, U5: 4093B; SOIC-14_3.9x8.7mm_P1.27mm
U2: 4027B; SOIC-16_3.9x9.9mm_P1.27mm
U6: 14538B; SOIC-16_3.9x9.9mm_P1.27mm
U7: MCP1799_3V3; SOT-23

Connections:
GND: C1.2, C3.1, C4.1, C5.2, C6.2, C8.2, C9.2, C10.2, C11.2, C12.2, C13.2, C14.2, C15.2, H1.1, H2.1, H3.1, H4.1, J2.1, J3.2, J4.1, J5.2, R12.2, U1.7 (GND), U2.4 (R), U2.7 (S), U2.8 (VSS), U2.9 (S), U3.7 (GND), U5.7 (GND), U6.1 (Cx), U6.8 (VSS), U6.12 (Clk+), U6.15 (Cx), U7.1 (GND)
unnamed: C1.1, R1.2, U1.1
unnamed: C3.2, R4.1, U5.12, U5.13
unnamed: C9.1, R9.2, R10.2, U3.12
unnamed: C10.1, C11.1, D1.1 (K), R7.1, U7.3 (VI)
unnamed: D2.2 (A), D3.2 (A), J4.4
unnamed: D2.1 (K), J2.2, J5.1, R2.2, U3.6, U5.1, U5.2
unnamed: D3.1 (K), JP1.2 (C)
unnamed: D4.2 (A), U5.3
unnamed: D4.1 (K), D5.1 (K), R12.1, U1.2
unnamed: D5.2 (A), U2.15 (Q)
unnamed: F1.1, R7.2
unnamed: C2.2, J2.3, R3.2, U3.8
unnamed: J2.4, U3.3
unnamed: J3.3, R5.2, U6.4 (Clk+)
unnamed: F1.2, J4.2, J5.3
unnamed: J4.3, U3.4
unnamed: JP1.1 (A), U2.14 (~Q)
unnamed: JP1.3 (B), U2.13 (C), U5.4
unnamed: R1.1, U1.3, U1.5, U1.6, U1.8
unnamed: R4.2, U5.10
unnamed: R11.1, U5.6
unnamed: U1.10, U3.1
unnamed: U1.11, U3.2
unnamed: U1.4, U1.13
unnamed: U2.3 (C), U3.10, U5.5, U6.11 (Clk-)
unnamed: U1.9, U2.1 (Q), U5.8
unnamed: U1.12, U2.2 (~Q)
unnamed: U2.12 (R), U3.11, U5.9
unnamed: U3.5, U5.11
unnamed: C5.1, C6.1, R8.2, U6.2 (RxCx)
unnamed: R10.1, U6.7 (~Q)
unnamed: R11.2, U6.10 (Q)
unnamed: C8.1, R6.2, U6.14 (RxCx)
VDD: C2.1, C4.2, C12.1, C13.1, C14.1, C15.1, D1.2 (A), J3.1, R2.1, R3.1, R5.1, R6.1, R8.1, R9.1, U1.14 (VCC), U2.5 (K), U2.6 (J), U2.10 (J), U2.11 (K), U2.16 (VDD), U3.9, U3.13, U3.14 (VCC), U5.14 (VCC), U6.3 (R), U6.5 (Clk-), U6.13 (R), U6.16 (VDD), U7.2 (VO)

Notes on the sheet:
motor on/off logic see note <<<
regen on/off FF, double-click toggles, reset on pedaling
note: motor on/off logic motor is on (output low) if not braking, pedal assist is on, and pedaling fast enough otherwise, motor is off (output high)
pedal sensor (square wave 0-40hz)
rgn brk/mode (low=on)
double-click
pedal cadence sense see note <<<
accessory_gnd
button
pedal
button debounce
motor (low=on)
default pro, cut NC & solder NO for std
brake_in
pedal assist on/off FF, click toggles
LED (1.5ma max!)
battery power
install D5 for Pro kit only
install D2 for Pro kit only
double-click timer
~{brake}
brake_out
LED Behavior: pedal assist on, regen off: solid on pedal assist on, regen on (or actively braking): flashes pedal assist off, regen off: off pedal assist off, regen on (or actively braking): flashes
note: pedal cadence sense cadence threshold is nominally 40rpm on/29rpm off, with C6 installed, C5 uninstalled, and typical 4093 Vp/Vn values (Vp = 3.3, Vn = 2.3) install C5+C6 to lower threshold, or make up for 4093 Vp/Vn variation install C5 only to raise threshold, or make up for 4093 Vp/Vn vari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
pedal assist on
battery input PTC protection 3.3v linear regulator min current approx. 225ua max current approx. 3ma
accessory_pwr

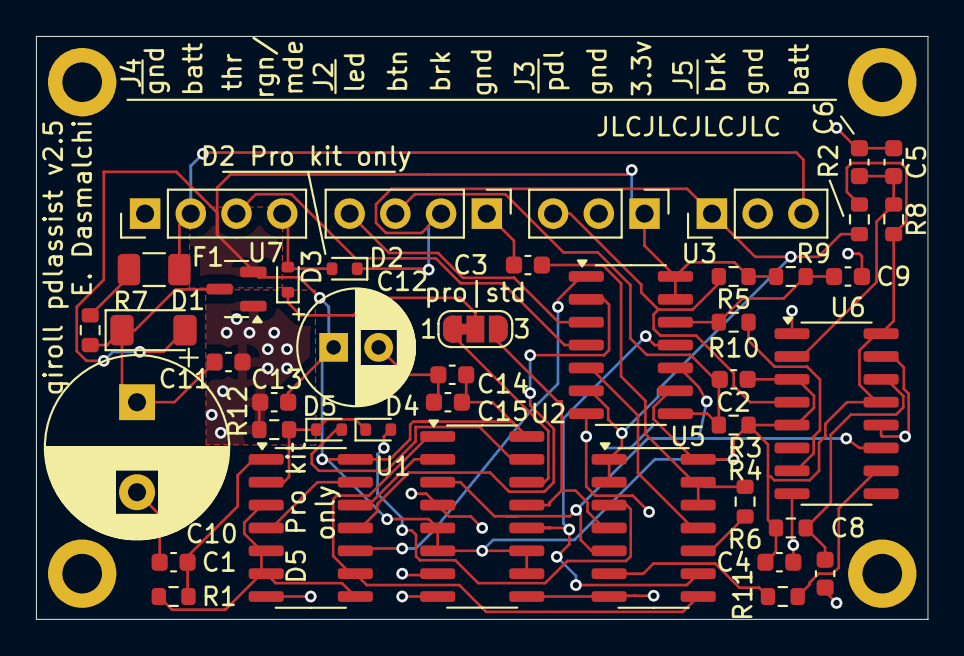
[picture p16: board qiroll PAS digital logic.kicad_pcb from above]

Board: 2 copper layers, 49.5 x 32.4 mm, 47 parts (0 on the bottom side), 35 nets.

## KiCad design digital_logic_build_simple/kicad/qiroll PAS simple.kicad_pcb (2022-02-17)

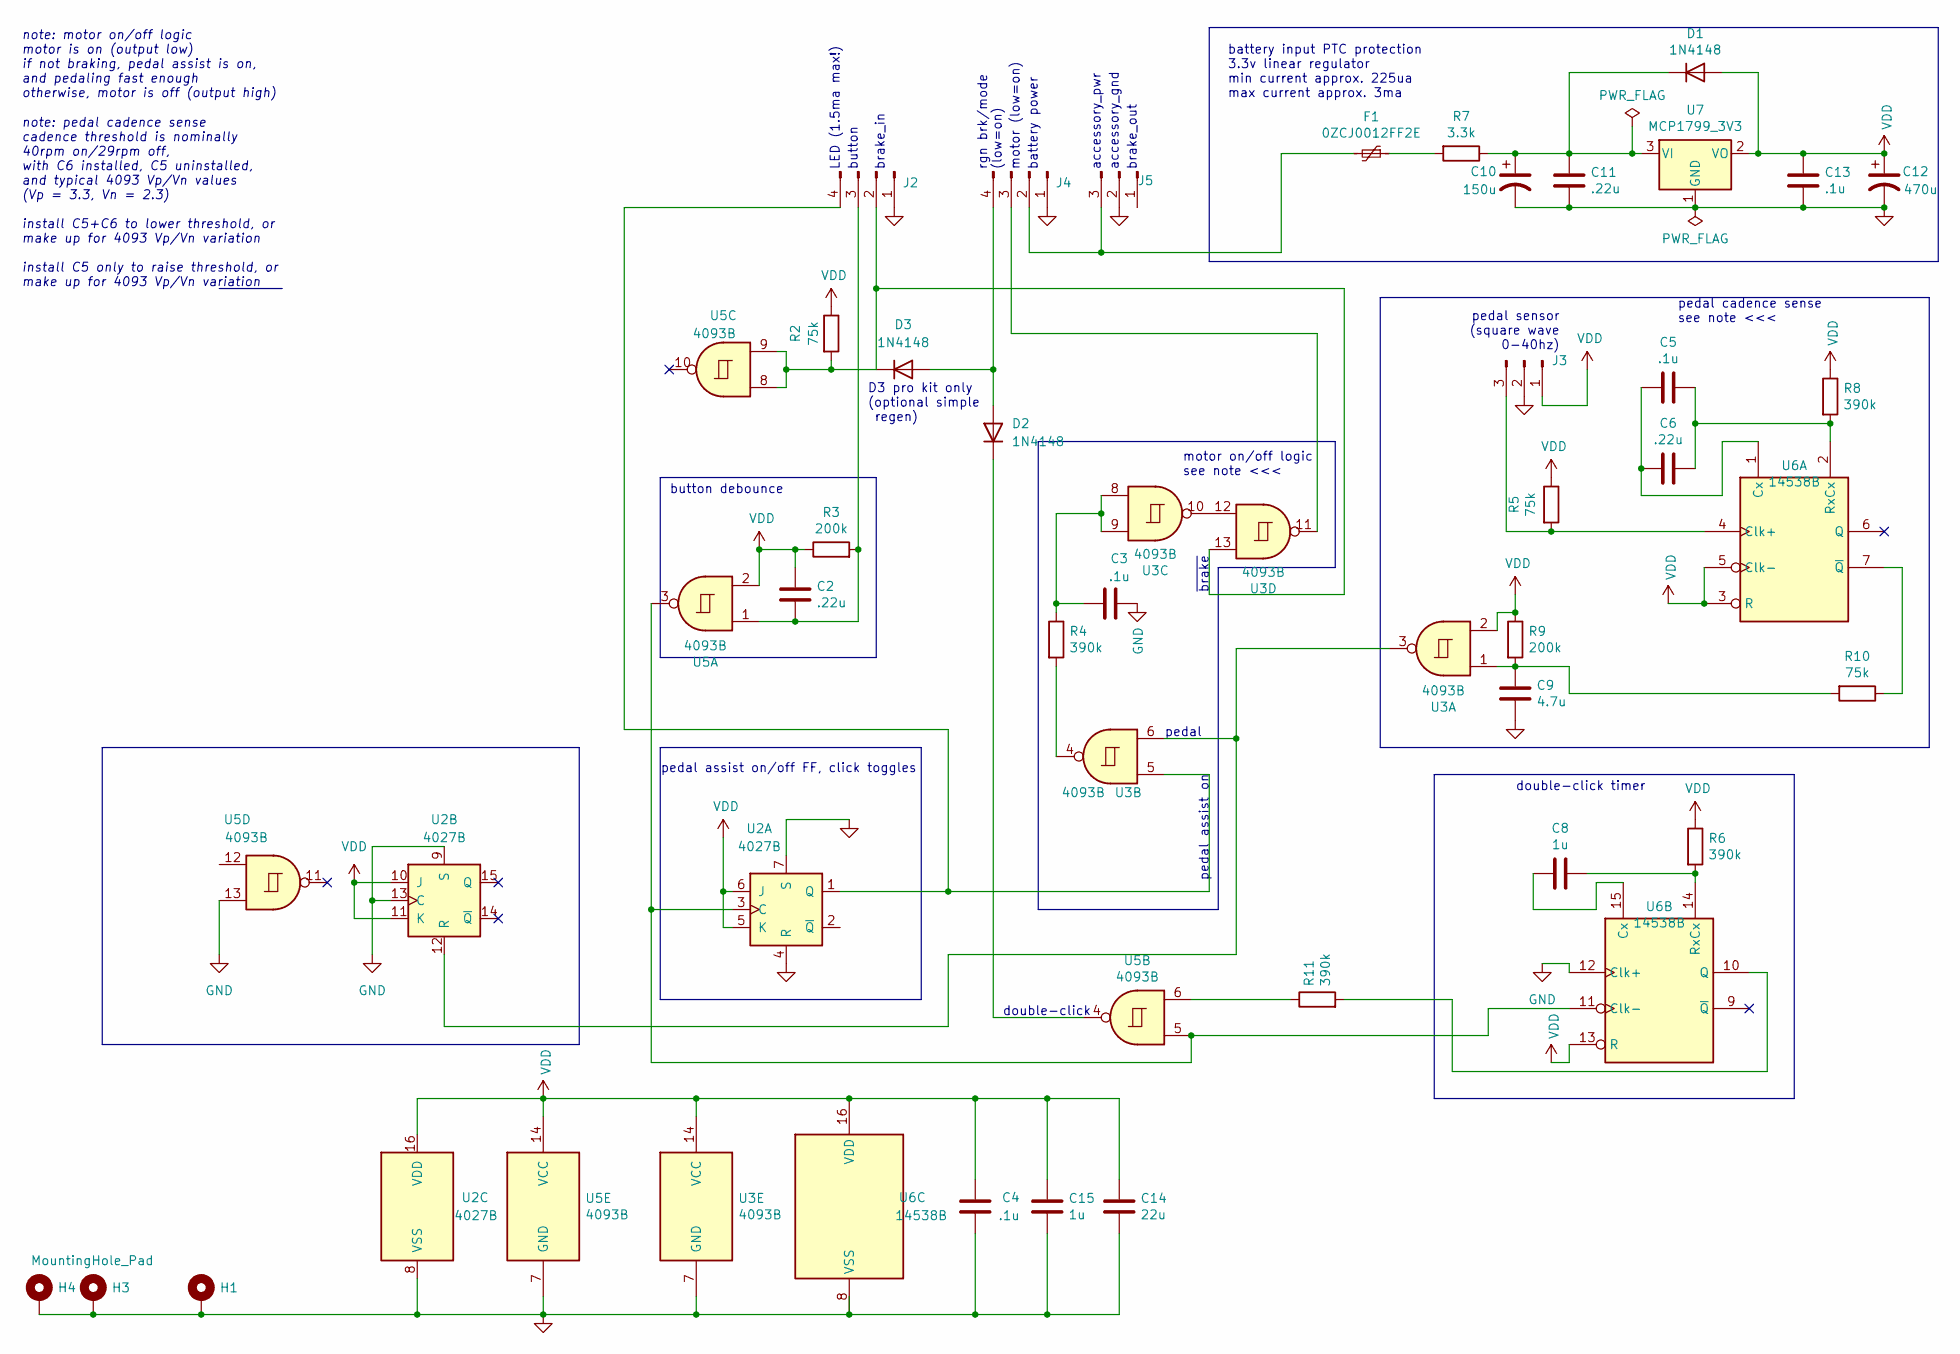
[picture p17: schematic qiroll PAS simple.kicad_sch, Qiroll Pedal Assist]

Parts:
C2, C6, C11: .22u; C_Rect_L4.6mm_W3.0mm_P2.50mm_MKS02_FKP02
C3, C4, C5, C13: .1u; C_Rect_L4.6mm_W3.0mm_P2.50mm_MKS02_FKP02
C8, C15: 1u; C_Rect_L4.6mm_W3.0mm_P2.50mm_MKS02_FKP02
C9: 4.7u; C_Rect_L4.6mm_W3.0mm_P2.50mm_MKS02_FKP02
C10: 150u; R_Axial_DIN0204_L3.6mm_D1.6mm_P5.08mm_Vertical
C12: 470u; CP_Radial_D6.3mm_P2.50mm
C14: 22u; CP_Radial_D5.0mm_P2.00mm
D1: 1N4148; D_DO-35_SOD27_P3.81mm_Vertical_AnodeUp
D2, D3: 1N4148; D_DO-35_SOD27_P7.62mm_Horizontal
F1: 0ZCJ0012FF2E; R_Axial_DIN0309_L9.0mm_D3.2mm_P5.08mm_Vertical
H1, H3, H4: MountingHole_Pad; MountingHole_2.2mm_M2_DIN965_Pad
J2: led_sw1; PinHeader_1x04_P2.54mm_Vertical
J3: accessory; PinHeader_1x03_P2.54mm_Vertical
J4: mode_thr_batt; PinHeader_1x04_P2.54mm_Vertical
J5: 3_pin; PinHeader_1x03_P2.54mm_Vertical
R2: 75k; R_Axial_DIN0207_L6.3mm_D2.5mm_P7.62mm_Horizontal
R3, R9: 200k; R_Axial_DIN0207_L6.3mm_D2.5mm_P2.54mm_Vertical
R4, R6, R8, R11: 390k; R_Axial_DIN0207_L6.3mm_D2.5mm_P2.54mm_Vertical
R5, R10: 75k; R_Axial_DIN0207_L6.3mm_D2.5mm_P2.54mm_Vertical
R7: 3.3k; R_Axial_DIN0207_L6.3mm_D2.5mm_P2.54mm_Vertical
U2: 4027B; DIP-16_W7.62mm
U3, U5: 4093B; DIP-14_W7.62mm
U6: 14538B; DIP-16_W7.62mm
U7: MCP1799_3V3; TO-92

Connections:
GND: C3.1, C4.1, C9.2, C10.2, C11.2, C12.2, C13.2, C14.2, C15.2, H1.1, H3.1, H4.1, J2.1, J3.2, J4.1, J5.2, U2.4 (R), U2.7 (S), U2.8 (VSS), U2.9 (S), U2.13 (C), U3.7 (GND), U5.7 (GND), U5.13, U6.8 (VSS), U6.12 (Clk+), U7.1 (GND)
unnamed: C2.2, J2.3, R3.2, U5.1
unnamed: C3.2, R4.1, U3.8, U3.9
unnamed: C5.1, C6.1, R8.2, U6.2 (RxCx)
unnamed: C5.2, C6.2, U6.1 (Cx)
unnamed: C8.1, R6.2, U6.14 (RxCx)
unnamed: C8.2, U6.15 (Cx)
unnamed: C9.1, R9.2, R10.2, U3.1
unnamed: C10.1, C11.1, D1.1 (K), R7.1, U7.3 (VI)
unnamed: D2.1 (K), U5.4
unnamed: D2.2 (A), D3.2 (A), J4.4
unnamed: D3.1 (K), J2.2, R2.2, U3.13, U5.8, U5.9
unnamed: F1.1, R7.2
unnamed: F1.2, J4.2, J5.3
unnamed: J2.4, U2.1 (Q), U3.5
unnamed: J3.3, R5.2, U6.4 (Clk+)
unnamed: J4.3, U3.11
unnamed: R4.2, U3.4
unnamed: R10.1, U6.7 (~Q)
unnamed: R11.1, U5.6
unnamed: R11.2, U6.10 (Q)
unnamed: U2.3 (C), U5.3, U5.5, U6.11 (Clk-)
unnamed: U2.12 (R), U3.3, U3.6
unnamed: U3.10, U3.12

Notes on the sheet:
motor on/off logic see note <<<
note: motor on/off logic motor is on (output low) if not braking, pedal assist is on, and pedaling fast enough otherwise, motor is off (output high)
pedal sensor (square wave 0-40hz)
rgn brk/mode (low=on)
double-click
pedal cadence sense see note <<<
accessory_gnd
button
pedal
button debounce
motor (low=on)
D3 pro kit only (optional simple regen)
brake_in
pedal assist on/off FF, click toggles
LED (1.5ma max!)
battery power
double-click timer
~{brake}
brake_out
note: pedal cadence sense cadence threshold is nominally 40rpm on/29rpm off, with C6 installed, C5 uninstalled, and typical 4093 Vp/Vn values (Vp = 3.3, Vn = 2.3) install C5+C6 to lower threshold, or make up for 4093 Vp/Vn variation install C5 only to raise threshold, or make up for 4093 Vp/Vn vari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
pedal assist on
battery input PTC protection 3.3v linear regulator min current approx. 225ua max current approx. 3ma
accessory_pwr

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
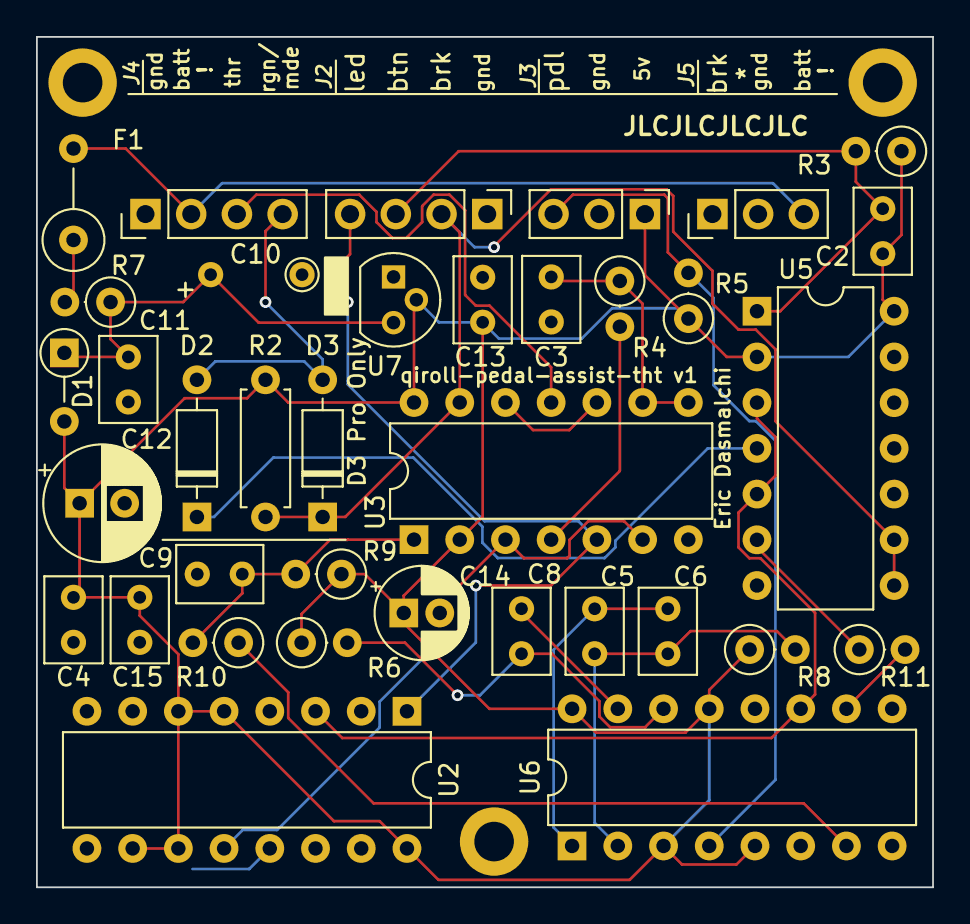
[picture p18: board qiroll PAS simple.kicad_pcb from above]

Board: 2 copper layers, 49.8 x 47.2 mm, 39 parts (0 on the bottom side), 25 nets.

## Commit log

2021-01-16 placed sketch in folder to placate Arduino IDE
2021-01-17 fixed bug preventing LED from turning off after pas mode turned off
2021-02-04 as-working on-bike with stripboard connector adaptor
2021-02-21 add aggressive debouncing to attiny85 version, kicad files for digital logic version (incomplete)
2021-02-21 add kicad files for digital logic version (unfinished)
    [qiroll PAS digital logic.kicad_pcb, qiroll PAS digital logic.sch]
2021-02-21 digital logic prototype kicad schematic, complete but untested
    [qiroll PAS digital logic.sch]
2021-02-21 fix schematic, export to png
    [qiroll PAS digital logic.kicad_pcb, qiroll PAS digital logic.sch]
2021-02-21 move kicad cache file
2021-02-22 fix arduino mode switch bug
2021-03-28 add rc debounce, decoupling
    [qiroll PAS digital logic.sch]
2021-03-28 update r1r2 values
    [qiroll PAS digital logic.sch]
2021-04-01 annotate schematic, voltage regulator, photos
    [qiroll PAS digital logic.sch]
2021-04-05 fix schematic errors, swap 4023 units for ease of assembly
    [qiroll PAS digital logic.sch]
2021-04-05 crop schematic
2021-04-05 match new schematic
2021-06-17 add electrolytic caps for stability
    [qiroll PAS digital logic.kicad_pcb, qiroll PAS digital logic.sch]
2021-06-20 add voltage reg caps to schematic.png, start work on v2
    [qiroll PAS digital logic.sch]
2021-06-28 pcb version 1, new features
    [qiroll PAS digital logic-B_Cu.gbl, qiroll PAS digital logic-B_Mask.gbs, qiroll PAS digital logic-Edge_Cuts.gm1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]
2021-07-02 add brake sensor pulldown, incomplete BOM
    [qiroll PAS digital logic.kicad_pcb, qiroll PAS digital logic.sch, qiroll PAS digital logic_bom_.csv]
2021-07-02 remove v1 gerbers
    [qiroll PAS digital logic-B_Cu.gbl, qiroll PAS digital logic-B_Mask.gbs, qiroll PAS digital logic-Edge_Cuts.gm1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]
2021-07-03 add ptc and protection diode for voltage reg
    [qiroll PAS digital logic.kicad_pcb, qiroll PAS digital logic.sch]
2021-07-12 revised pcb w/ ptc, protection diode, revised c11 value
    [qiroll PAS digital logic.kicad_pcb, qiroll PAS digital logic.sch]
2021-07-14 pcb revision, add circuit sim, old kicad files to reference for v1 board repairs
    [qiroll PAS digital logic-B_Cu.gbl, qiroll PAS digital logic-B_Mask.gbs, qiroll PAS digital logic-Edge_Cuts.gm1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]
2021-07-17 add old design safety notes, delete faulty gerbers
    [qiroll PAS digital logic-B_Cu.gbl, qiroll PAS digital logic-B_Mask.gbs, qiroll PAS digital logic-Edge_Cuts.gm1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]
2021-07-20 more Schmitt triggers\!
    [qiroll PAS digital logic.sch]
2021-07-20 trial component placement
    [qiroll PAS digital logic.kicad_pcb, qiroll PAS digital logic.sch]
2021-07-23 v2 PCB for review/manufacture
    [qiroll PAS digital logic.dsn, qiroll PAS digital logic.kicad_pcb, qiroll PAS digital logic.sch]
2021-07-23 add v2 gerbers, pending review
    [qiroll PAS digital logic-B_Cu.gbl, qiroll PAS digital logic-B_Mask.gbs, qiroll PAS digital logic-Edge_Cuts.gm1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]
2021-07-30 v2 PCB for production
    [qiroll PAS digital logic-B_Cu.gbl, qiroll PAS digital logic-B_Mask.gbs, qiroll PAS digital logic-Edge_Cuts.gm1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]
2021-09-04 add case CAD files, 3d print instructions for Creality Ender
    [bottom_case.scad, bottom_case.stl, case_test.scad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]
2021-09-04 schematic naming
2021-10-16 pcb version 2.2, hopefully fixes brake input/mode instablity
    [qiroll PAS digital logic-B_Cu.gbl, qiroll PAS digital logic-B_Mask.gbs, qiroll PAS digital logic-Edge_Cuts.gm1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]
2021-10-16 add v2.2 schematic
2021-10-18 remove old files, add new schematic
    [qiroll PAS digital logic.dsn, qiroll PAS digital logic_bom_.csv]
2021-10-18 actually add schematic
2021-10-20 fix brake label, a more connected ground plane
    [qiroll PAS digital logic-B_Cu.gbl, qiroll PAS digital logic-B_Mask.gbs, qiroll PAS digital logic-Edge_Cuts.gm1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]
2021-11-20 remove arduino
2021-11-20 new folder
    [bottom_case.scad, bottom_case.stl, case_test.scad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]
2021-11-20 remove old
    [bottom_case.scad, bottom_case.stl, case_test.scad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]
2021-12-15 version 2.5
    [bottom_case.scad, bottom_case.stl, qiroll PAS digital logic.kicad_pcb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]
2021-12-15 gerbers and schematic
    [qiroll PAS digital logic-B_Cu.gbl, qiroll PAS digital logic-B_Mask.gbs, qiroll PAS digital logic-Edge_Cuts.gm1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]
2021-12-16 better bike photo
    [qiroll PAS digital logic.sch]
2021-12-16 add digikey bom
    [digikey_v2.5_parts.csv]
2021-12-17 clarify silkscreen
    [qiroll PAS digital logic-B_Cu.gbl, qiroll PAS digital logic-B_Mask.gbs, qiroll PAS digital logic-Edge_Cuts.gm1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]
2021-12-18 even tidier schematic
    [qiroll PAS digital logic-B_Cu.gbl, qiroll PAS digital logic-B_Mask.gbs, qiroll PAS digital logic-Edge_Cuts.gm1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]
2022-02-17 add simple, update main pcb to KiCad 6
    [bottom_case.scad, bottom_case.stl, case_test.scad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]
2022-02-17 fix simple schematic, delete old files
    [qiroll PAS digital logic-B_Cu.gbl, qiroll PAS digital logic-B_Mask.gbs, qiroll PAS digital logic-Edge_Cuts.gm1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]
2024-06-12 update pcb to new kicad
    [qiroll PAS digital logic.kicad_pcb, qiroll PAS digital logic.kicad_sch]
2024-06-26 revise footprints
    [qiroll PAS digital logic.kicad_pcb]
2024-06-26 bigger silkscreen
    [qiroll PAS digital logic.kicad_pcb]
2024-06-27 new gerbers
    [qiroll PAS digital logic-B_Cu.gbl, qiroll PAS digital logic-B_Mask.gbs, qiroll PAS digital logic-Edge_Cuts.gm1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]
